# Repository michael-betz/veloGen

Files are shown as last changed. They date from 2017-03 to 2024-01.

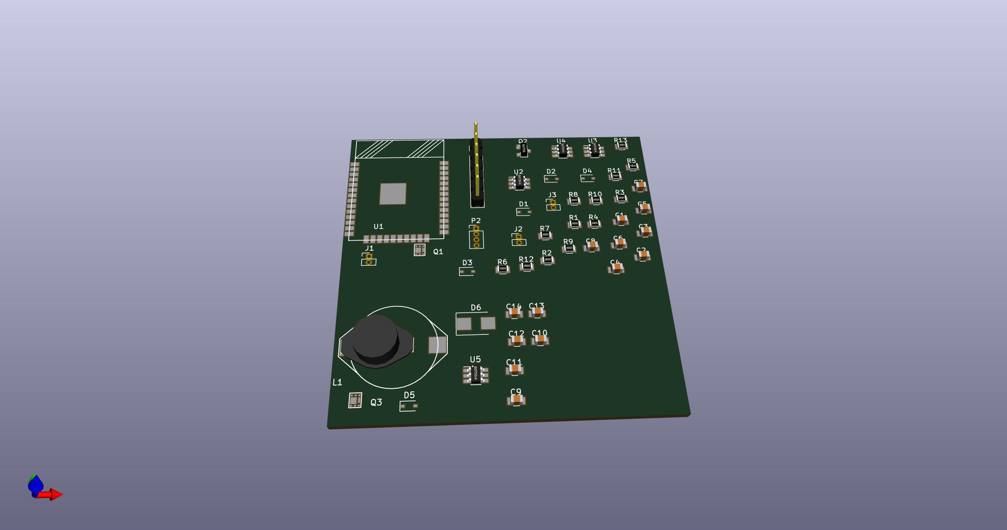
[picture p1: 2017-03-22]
PCB/3D_progress/01.jpg

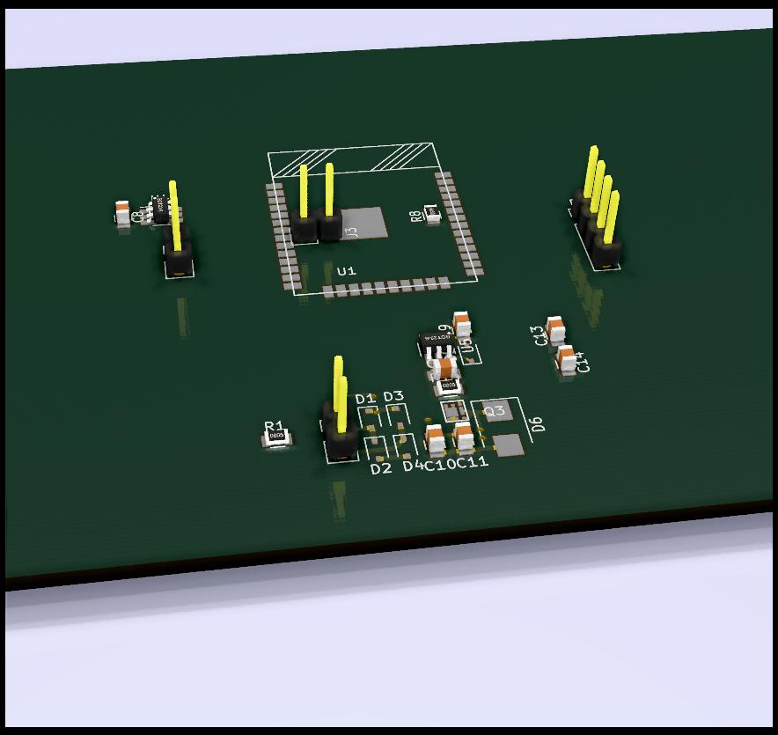
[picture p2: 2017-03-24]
PCB/3D_progress/03.jpg

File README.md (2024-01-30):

# veloGen
Minimalist bike computer and hub dynamo power manager.

A typical hub dynamo can deliver approx. 6 - 10 V at 0.5 A. Output current is inductively limited and stays relatively stable over speed. However voltage will go up. A custom made buck converter is used to extract maximum power and charge a 18650 liion cell. The front and back bike lights will be powered by this cell.

Speed and distance is tracked by measuring the zero crossings of the hub dynamo AC output. Data is collected in the CPU until read out by a mobile device over bluetooth and possibly published to a cloud service.

# Brainstorming

 * Will use ESP-WROOM-32 and make good use of the sleep modes
 * AC input zero crossing --> falling edge interrupt. Wake up CPU and increment counting reg.
 * Every second, keep track of:
   * Battery voltage. --> ADC + voltage divider to 3 V
   * Generator RMS(or peak) voltage. --> ADC + voltage divider to 3 V
   * Generator RMS current. --> 5 mOhm shunt + TS1101 + ADC 1 V
   * Battery current in and out --> 5 mOhm shunt + TS1101 + ADC 1 V
   * Realtime clock timestamp
* Store these datasets in a circular buffer in memory, until read out over BLE.
* Manage the Buck converter PWM to charge the battery with maximum current

## PCB

 * 3.3 V LDO
 * WROOM-32
 * Buck inductor
 * Buck Schottky: STPS3L40UF
 * High side mosfet driver: LTC4440-5 in SOT-23
 * High side Mosfet: STL6N3LLH6
 * 4 x schottky diode for bridge rectifier
 * Smoothing cap (10 uF?)
 * 2 x current sensing shunt (Igenerator, Ibattery) + 2 x TS1101
 * IN system programming pins
 * P - channel mosfet to switch off external power on fault (low battery / overcurrent)

### Datasheets
 * [MCP1630](http://ww1.microchip.com/downloads/en/DeviceDoc/21896b.pdf)
 * [LiIon app note](http://ww1.microchip.com/downloads/en/DeviceDoc/51555b.pdf)

## 3D printed case

 * Mounts with zip ties / verlcro straps on the frame between 2 tubes angeled at 120 deg
 * 2 Shellswhich clip / screw together
 * 5 mm wall thickness with a groove to place an O-ring between the shells
 * AC input cable (2 pin)
 * DC output + I2C cable (4 pin)

# Rev1 Notes
  * Need mounting holes on PCB
  * Case clamping the PCB doesn't work like that
  * Case make teeth tighter
  * Need to find less huge connectors for battery, dynamo and I2C
  * Add OLED to case (Case and PCB can be made wider)

# Bringup (rev1)
  * connect pogo pin adapter to board and USB serial cable
  * force flash voltage to 3.3V

```bash
$ espefuse.py set_flash_voltage 3.3V
espefuse.py v2.7
Connecting........_____....._
Enable internal flash voltage regulator (VDD_SDIO) to 3.3V.
The following efuses are burned: XPD_SDIO_FORCE, XPD_SDIO_REG, XPD_SDIO_TIEH.
This is an irreversible operation.
Type 'BURN' (all capitals) to continue.
BURN
VDD_SDIO setting complete.

$ esptool.py flash_id
esptool.py v2.7
Found 1 serial ports
Serial port /dev/ttyUSB0
Connecting........__
Detecting chip type... ESP32
Chip is ESP32D0WDQ5 (revision 1)
Features: WiFi, BT, Dual Core, 240MHz, VRef calibration in efuse, Coding Scheme None
Crystal is 40MHz
MAC: 40:f5:20:5c:8d:48
Uploading stub...
Running stub...
Stub running...
Manufacturer: c8
Device: 4018
Detected flash size: 16MB
Hard resetting via RTS pin..
```

  * `pio run -t uploadfs`
  * `pio run -t upload -t monitor`

You should see velogen booting up in the terminal.

# Changes to add for REV2

  * add 200k pulldown and 10 nF RC filter to speed sense pin
  * add Zener diode across supply rail
  * real buttons
  * better connectors (waterproofing)
  * Switchable battery power output for front light?
  * Switchable 5 V output for WS2812

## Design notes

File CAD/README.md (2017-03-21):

# Some notes about the case
  * Some kind of strapping system to attach to bike frame
  * Make the case slightly parametric to adapt to angles / dimensions of different bike frames
  * Case needs to be at least splash - waterproof
    * That means some kind of gasket / o-ring between the half shells
  * Waterproof PCB connectors? Never saw such a thing
    * AC input
    * DC out (to front light)
    * DC out (to back light)
    * Maybe just one DC out and split externally
  * Model the whole thing in Fusion360? Is there an open source alternative?

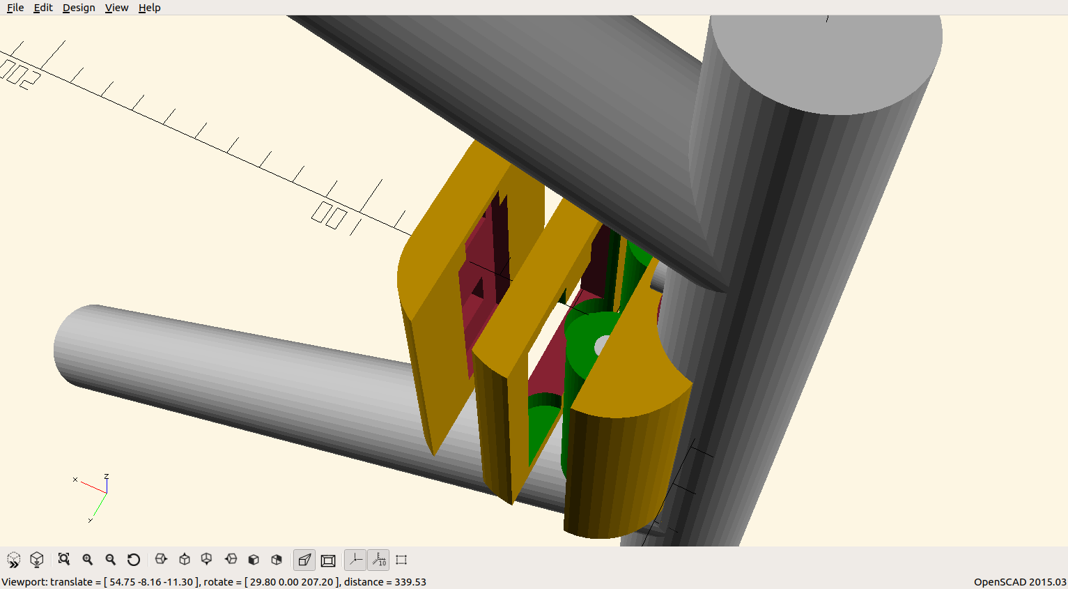
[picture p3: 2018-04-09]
CAD/scr.png

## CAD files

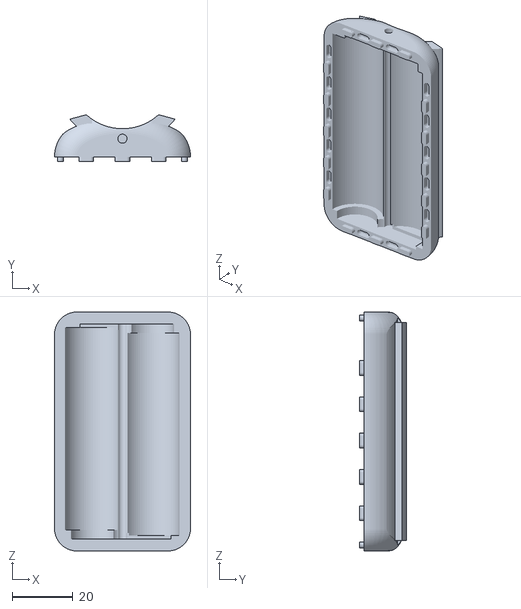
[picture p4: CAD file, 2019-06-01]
CAD/lipoShell4_lower.stl
45.0 x 15.4 x 79.0

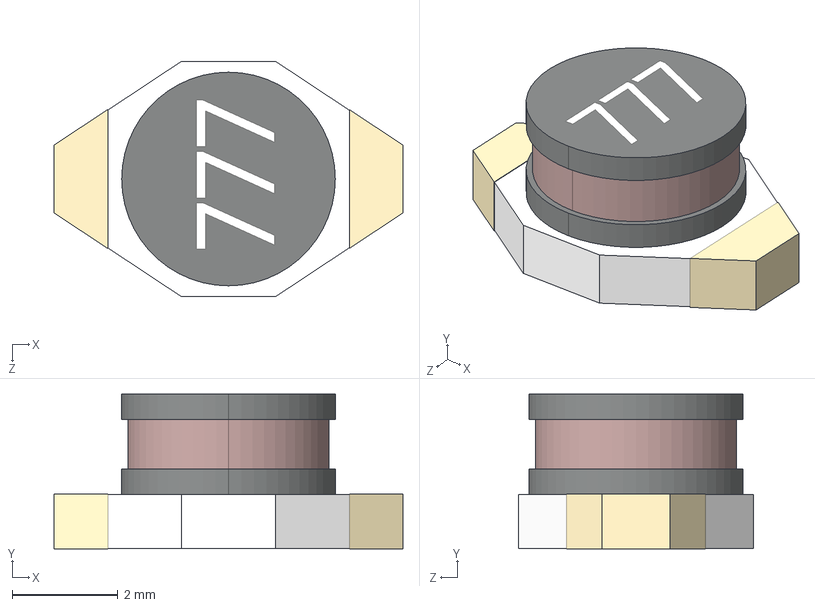
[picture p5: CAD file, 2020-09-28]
PCB2/Coilcraft-DO1608C.step
6.60 x 2.93 x 4.45 mm

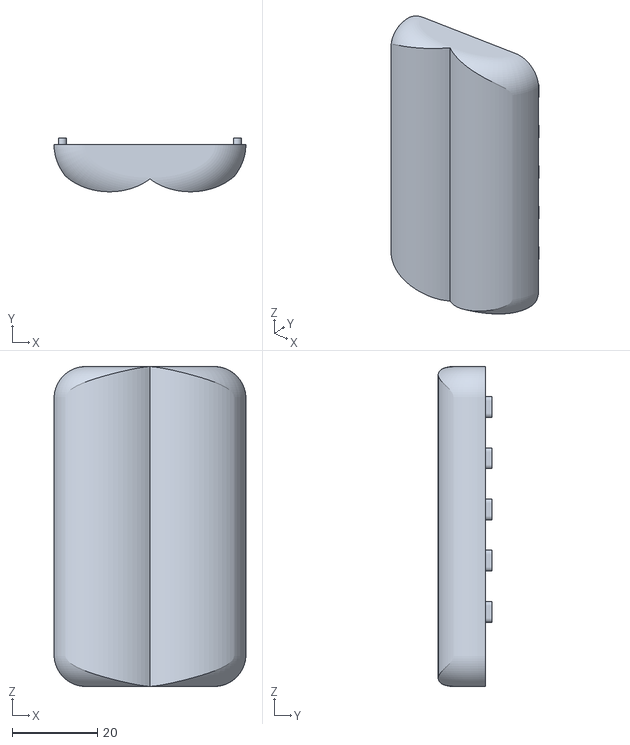
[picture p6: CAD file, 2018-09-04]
CAD/lipoShell3_upper.stl
45.0 x 12.6 x 75.0

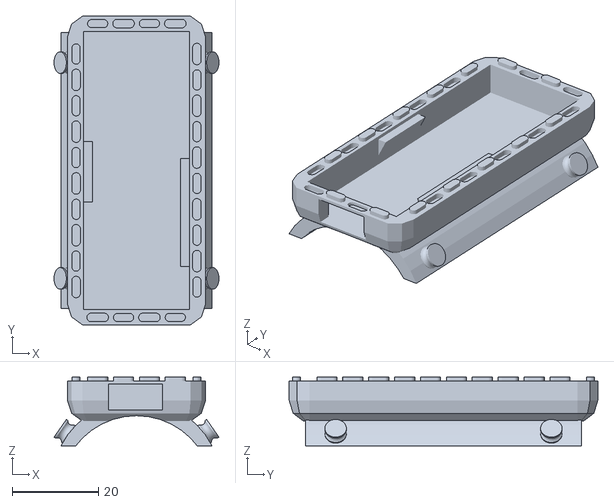
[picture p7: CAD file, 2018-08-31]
CAD/pcbShell_lower.stl
38.2 x 71.5 x 15.9

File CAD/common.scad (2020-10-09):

$fn=75;

// Bike frame mock-up
rPipe = 35.4 / 2;  // vertical pipe
// rPipe = 32.1 / 2; // horizontal pipe

module bikeFrame() {
  color("DarkGray") union() {
    // Frame
    cylinder(h=250, r=rPipe, center=true);
    translate([0,0,-(50+rPipe)]) rotate([0,120,0]) cylinder(h=300, r=rPipe);
    translate([0,0, (50+rPipe)]) rotate([0, 70,0]) cylinder(h=300, r=rPipe);
    // Nipple
    translate([0,0, 50-15]) rotate([0, 90,0]) cylinder(h=20, r=5);
  }
}

// To generate the interlocking teeth between half shells
module teeth(scaleF=1.0, n=20, raster=12) {
  for (i = [0:n-1]){
    xTooth = (i - (n - 1) / 2) * raster;
    translate([xTooth,0,0]) scale(scaleF) union(){
        translate([1.5, 0, 0]) cylinder(h=3, r=1, center=true);
        cube(size=[3, 2, 3], center=true);
        translate([-1.5, 0, 0]) cylinder(h=3, r=1, center=true);
    }
  }
}

module pin(){
    difference(){
        cylinder(r=2.5, h=4.5);
        // Donut
        translate([0, 0, 3.2]) rotate_extrude() translate([3, 0, 0]) circle(r=1);
        // translate([-5, 0, 6]) rotate([0, 45, 0]) cube(size=[10, 10, 10], center=true);
    }
}

// D shaped, shall conform to bike frame
module holder(r_outer){
    difference(){
        union(){
            translate([0, 0, -9]) rotate([90, 0, 0]) cylinder(r=r_outer+2, h=64, center=true);
            // translate([-15.0,  25, 0]) rotate([0, -65, 0]) pin();
            // translate([-15.0, -25, 0]) rotate([0, -65, 0]) pin();
            // translate([ 15.0,  25, 0]) rotate([0,  65, 0]) pin();
            // translate([ 15.0, -25, 0]) rotate([0,  65, 0]) pin();
        }
        translate([0, 0, -25]) cube(size=[50, 100, 50], center=true);
    }
}

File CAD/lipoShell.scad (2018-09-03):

include<common.scad>

// Lipo battery mockup
module lipo() {
  union() {
    color("green") cylinder(h=65.75, r=18.5/2, center=true);
    color("silver") translate([0,0,65.75/2]) cylinder(h=1, r=4, center=true);
  }
}


module lipoInnerSpace(){
  scale(1.02) translate([0, 0, 33]) lipo();
  scale(1.02) translate([0, 0, -33]) lipo();
}


module lipoHalfShell(cylOffset=0, isMirror=false){
  difference(){
    // Outer shell
    minkowski(){
      translate([0, cylOffset, 0]) cylinder(h=125, r=5, center=true);
      sphere(10);
    }
    // Cut in half
    translate([0, -15, 0]) cube(size=[30, 30, 200], center=true);
    // Inner spaces
    if(isMirror){
      mirror([0, 0, 1]) lipoInnerSpace();
    } else {
      lipoInnerSpace();
    }
    // Teeth holes
    translate([-12.5, 0, -3]) rotate([90, 90, 0]) scale([1, 1, 1.2]) teeth(n=11);
    translate([ 12.5, 0,  3]) rotate([90, 90, 0]) scale([1, 1, 1.2]) teeth(n=11);
  }
  // Teeth
  translate([-12.5, 0,  3]) rotate([90, 90, 0]) teeth(0.94, n=11);
  translate([ 12.5, 0, -3]) rotate([90, 90, 0]) teeth(0.94, n=11);
}

module lipoShell(){
  difference(){
    lipoHalfShell(4);
    // Bike frame cutout
    translate([0, 28, 0]) cylinder(h=200, r=rPipe, center=true);
  }
  %translate([0, 0, 0]) rotate([180, 0, 0]) lipoHalfShell(-4, isMirror=true);
  // Lipo Mockup
  // translate([0, 0, -33.1]) lipo();
  // translate([0, 0,  33.1]) lipo();
}

lipoShell();

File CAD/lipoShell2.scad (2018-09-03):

include<common.scad>
cylOffset=7;

// Lipo battery mockup
module lipo() {
  union() {
    color("green") cylinder(h=65.75, r=18.5/2, center=true);
    color("silver") translate([0,0,65.75/2]) cylinder(h=1, r=4, center=true);
  }
}

module outerSkin(){
  minkowski(){
      translate([0, cylOffset, 0]) cylinder(h=60, r=8, center=true);
      sphere(15);
  }
}

module lipoHalfShell(isMirror=false){
  difference(){
    // Outer shell
    outerSkin();
    // Cut in half
    // translate([0, -50, 0]) cube(size=[100, 100, 100], center=true);
    // Inner spaces
    scale(0.95) hull() case2();
    translate([-10, 0, 0]) lipo();
    translate([ 10, 0, 0]) lipo();
  }
}

module lipoShell(){
  difference(){
    lipoHalfShell(-7);
    // Bike frame cutout
    translate([0, 26, 0]) cylinder(h=200, r=rPipe, center=true);
  }
  // %translate([0, 0, 0]) rotate([180, 0, 0]) lipoHalfShell(-4, isMirror=true);
  // Lipo Mockup
  // translate([0, 0, -33.1]) lipo();
  // translate([0, 0,  33.1]) lipo();
}

module case1(){
  difference(){
    translate([11.1, 18, 53]) rotate([0, 90, 180]) import("./battery holder/files/18650_V2.STL");
    translate([0, 0, 53]) cube(size=[30, 40, 20], center=true);
  }
}

module case2(){
  intersection(){
    difference(){
      union() {
        translate([-10.5, 0, 0]) case1();
        translate([ 10.5, 0, 0]) case1();
      }
      translate([0, -15, 10]) cube(size=[0.5, 20, 50], center=false);
    }
    scale(0.95) outerSkin();
  }
}



intersection(){
  union(){
    case2();
    // lipoHalfShell();
  }
  // translate([0, 100, 30]) cube(size=[200, 200, 50], center=true);
}

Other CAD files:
CAD/lipoShell3.scad
CAD/lipoShell4.scad
CAD/main.scad
CAD/pcbShell.scad
CAD/test.scad

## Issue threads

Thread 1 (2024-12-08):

current state of the project and feature ideas

cl0rm, 2024-12-08:
Hi,

how is the current state of this project? Does it run somewhat well / stable?
I'm developing hardware as well as software/firmware so I should be able to contribute here.

I've always wanted to build something very similar to this myself.

Two extra features that might be useful would be
- google "find my" integration as soon as more information is available about it (specs are open AFAIK- contrary to apple's implementation)
- maybe GPS tracking. I've build custom GPS devices using ublox modules in the past, the hardware implementation is rather straight forward and the energy usage moderate, but it requires rather large antennas to be useful

michael-betz, 2025-01-07:
Hi!

> how is the current state of this project? Does it run somewhat well / stable?

I have it on one of my bikes and it runs stable there.

I'm happy with the animated rear-light feature, changing color / animation as a function of speed.

Online telemetry over MQTT works well as long as the ESP is connected to a hotspot.
I never got the offline caching to work reliably (the flash would corrupt after a few weeks) and turned it off.

There are still many things on the TODO list ...

I wanted to see if I can send a few kB of data back on public WIFI hot-spots using DNS tunneling.

If that works, the idea was to implement tracking based on a log of received SSIDs. But this would require to solve the corrupted flash issue first.

Another thing that I haven't quite figured out yet is how to fully waterproof the electronics and especially the connectors while keeping everything compact.

Anyway, happy to see you are interested and I love your ideas! Feel free to use my code as a starting point.

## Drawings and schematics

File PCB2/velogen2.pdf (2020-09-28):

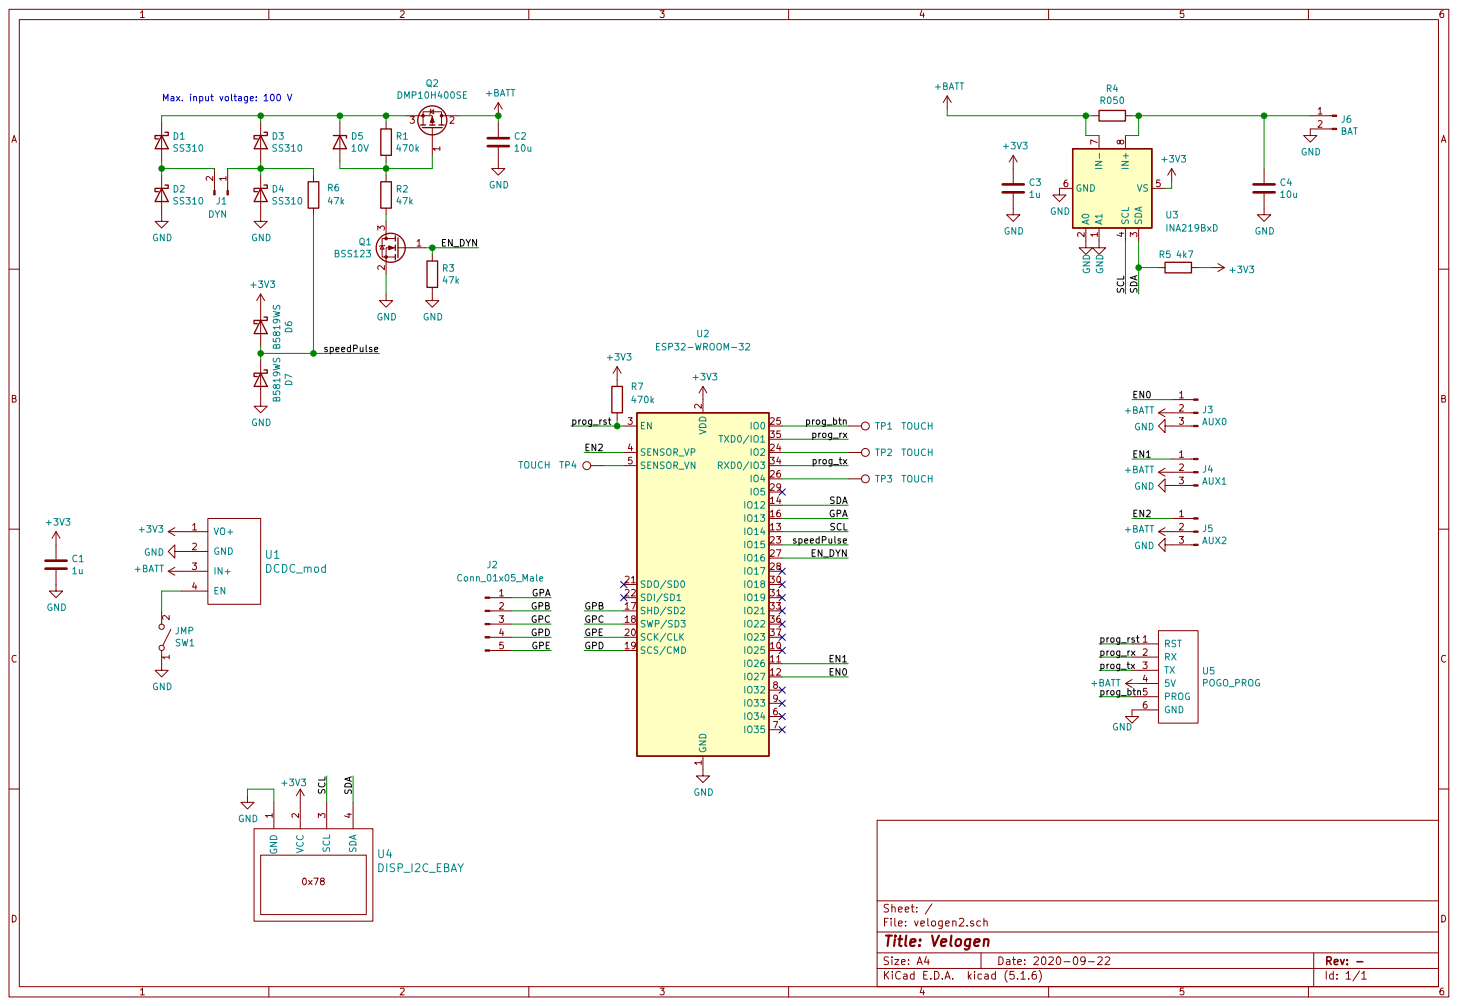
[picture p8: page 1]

4 VS 5 GND 6 IN- 7 IN+

2 SCK/CLK 20 SDO/SD0 21 SDI/SD1 22

JMP GND
File: velogen2.sch Sheet: / +BATT

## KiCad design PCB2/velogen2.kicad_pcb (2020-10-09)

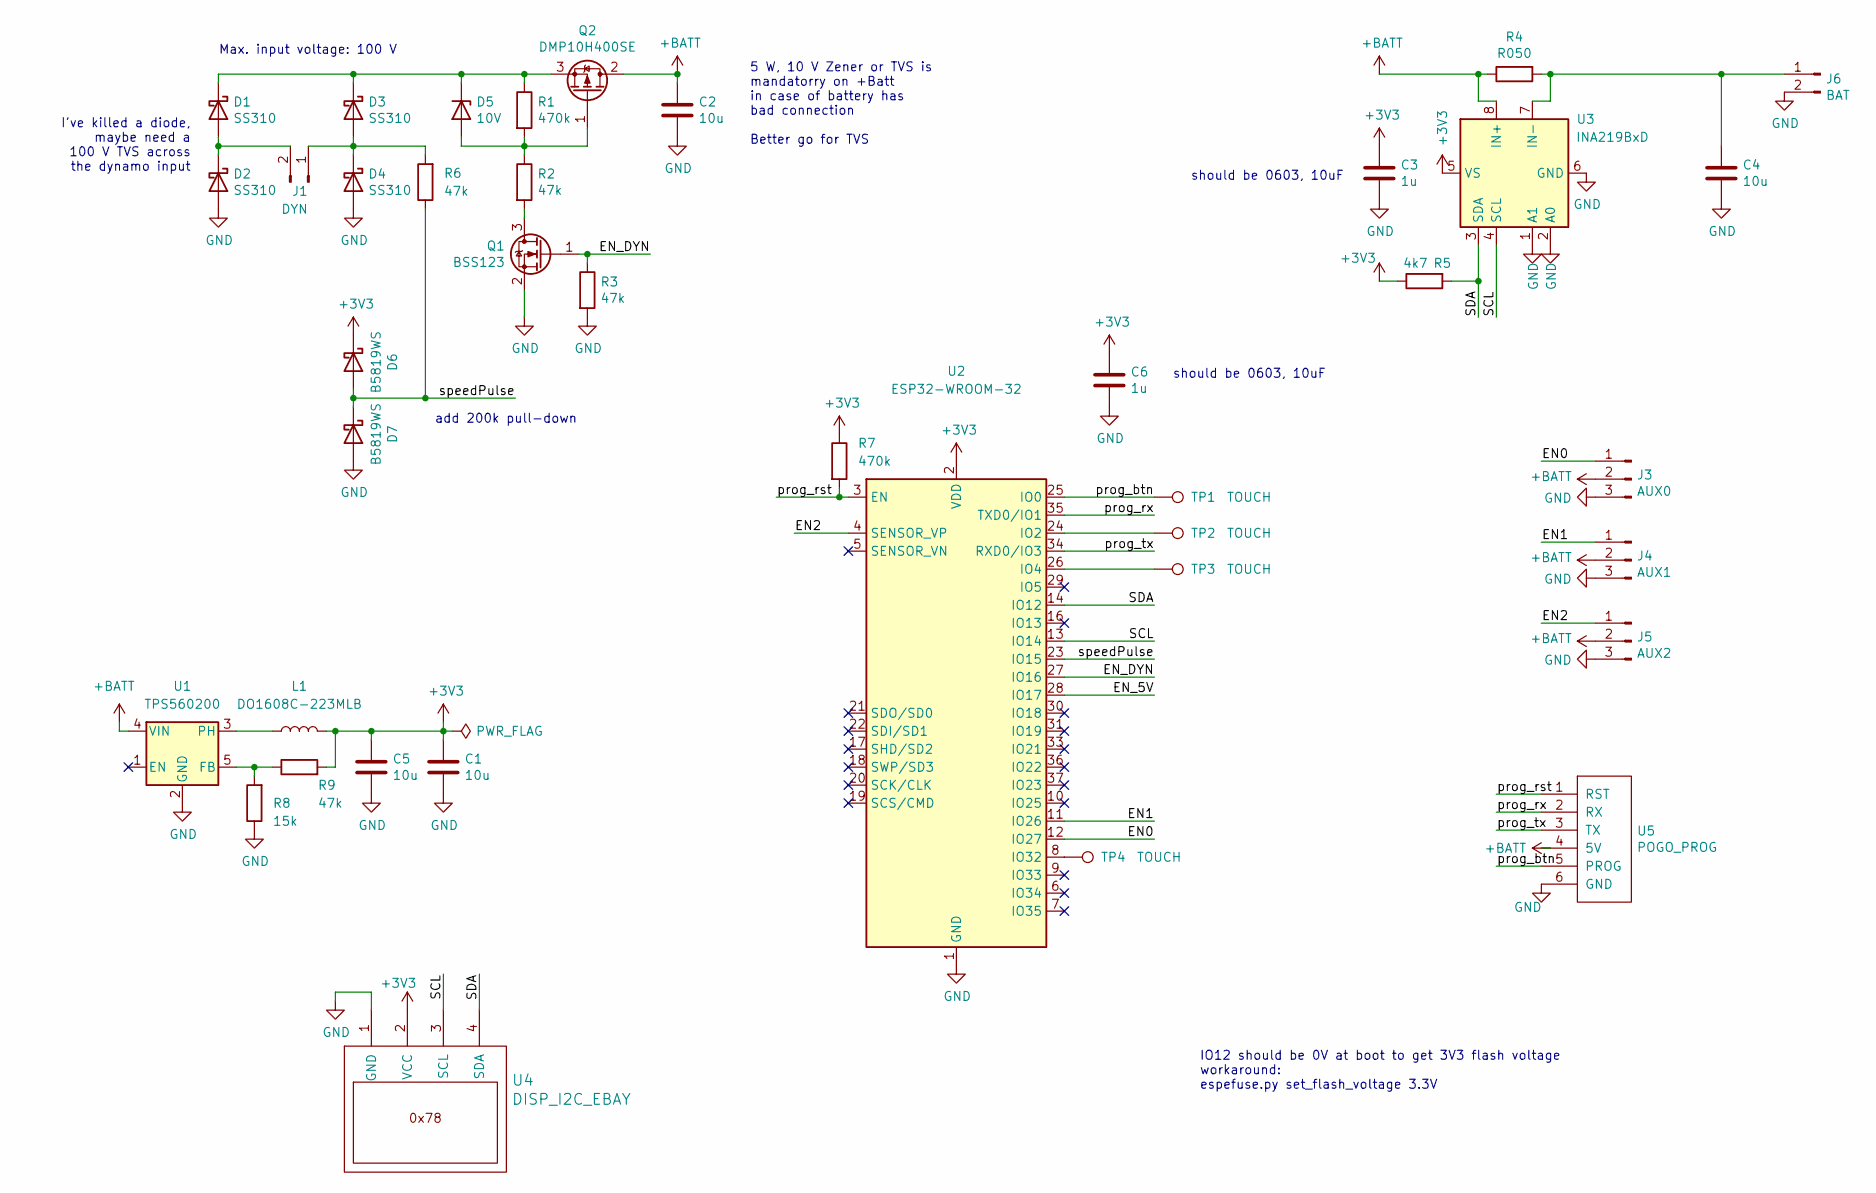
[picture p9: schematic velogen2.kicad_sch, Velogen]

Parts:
C1, C5: 10u; C_0603_1608Metric
C2, C4: 10u; C_1210_3225Metric
C3, C6: 1u; C_0805_2012Metric
D1, D2, D3, D4: SS310; D_SMA
D5: 10V; D_SOD-123
D6, D7: B5819WS; D_SOD-323
J1: DYN; JST_XH_S2B-XH-A-1_1x02_P2.50mm_Horizontal
J3: AUX0; JST_XH_S3B-XH-A-1_1x03_P2.50mm_Horizontal
J4: AUX1; JST_XH_S3B-XH-A-1_1x03_P2.50mm_Horizontal
J5: AUX2; JST_XH_S3B-XH-A-1_1x03_P2.50mm_Horizontal
J6: BAT; JST_XH_S2B-XH-A-1_1x02_P2.50mm_Horizontal
L1: DO1608C-223MLB; DO1608
Q1: BSS123; SOT-23
Q2: DMP10H400SE; SOT-223-3_TabPin2
R1, R7: 470k; R_0805_2012Metric
R2, R3, R6, R9: 47k; R_0805_2012Metric
R4: R050; R_1206_3216Metric
R5: 4k7; R_0805_2012Metric
R8: 15k; R_0805_2012Metric
TP1, TP2, TP3, TP4: TOUCH; TestPoint_THTPad_D1.5mm_Drill0.7mm
U1: TPS560200; SOT-23-5
U2: ESP32-WROOM-32
U3: INA219BxD; SOIC-8_3.9x4.9mm_P1.27mm
U4: DISP_I2C_EBAY
U5: POGO_PROG; myPogoPads

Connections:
+3V3: C1.1, C3.1, C5.1, C6.1, D6.1 (K), L1.2, R5.1, R7.1, R9.2, U2.2 (VDD), U3.5 (VS), U4.2 (VCC)
+BATT: C2.1, J3.2, J4.2, J5.2, Q2.2 (D), R4.1, U1.4 (VIN), U3.8 (IN+), U5.4 (5V)
/EN0: J3.1, U2.12 (IO27)
/EN1: J4.1, U2.11 (IO26)
/EN2: J5.1, U2.4 (SENSOR_VP)
/EN_DYN: Q1.1 (G), R3.1, U2.27 (IO16)
/SCL: U2.13 (IO14), U3.4 (SCL), U4.3 (SCL)
/SDA: R5.2, U2.14 (IO12), U3.3 (SDA), U4.4 (SDA)
/prog_btn: TP1.1, U2.25 (IO0), U5.5 (PROG)
/prog_rst: R7.2, U2.3 (EN), U5.1 (RST)
/prog_rx: U2.35 (TXD0/IO1), U5.2 (RX)
/prog_tx: U2.34 (RXD0/IO3), U5.3 (TX)
/speedPulse: D6.2 (A), D7.1 (K), R6.1, U2.23 (IO15)
GND: C1.2, C2.2, C3.2, C4.2, C5.2, C6.2, D2.2 (A), D4.2 (A), D7.2 (A), J3.3, J4.3, J5.3, J6.2, Q1.2 (S), R3.2, R8.1, U1.2 (GND), U2.1 (GND), U2.15 (GND), U2.38 (GND), U2.39 (GND), U3.1 (A1), U3.2 (A0), U3.6 (GND), U4.1 (GND), U5.6 (GND)
unnamed: C4.1, J6.1, R4.2, U3.7 (IN-)
unnamed: D1.1 (K), D3.1 (K), D5.1 (K), Q2.3 (S), R1.1
unnamed: D1.2 (A), D2.1 (K), J1.2
unnamed: D3.2 (A), D4.1 (K), J1.1, R6.2
unnamed: D5.2 (A), Q2.1 (G), R1.2, R2.1
unnamed: L1.1, U1.3 (PH)
unnamed: Q1.3 (D), R2.2
unnamed: R8.2, R9.1, U1.5 (FB)
unnamed: TP2.1, U2.24 (IO2)
unnamed: TP3.1, U2.26 (IO4)
unnamed: TP4.1, U2.8 (IO32)

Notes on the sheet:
IO12 should be 0V at boot to get 3V3 flash voltage workaround: espefuse.py set_flash_voltage 3.3V
add 200k pull-down
5 W, 10 V Zener or TVS is mandatorry on +Batt in case of battery has bad connection Better go for TVS
should be 0603, 10uF
I've killed a diode, maybe need a 100 V TVS across the dynamo input
Max. input voltage: 100 V

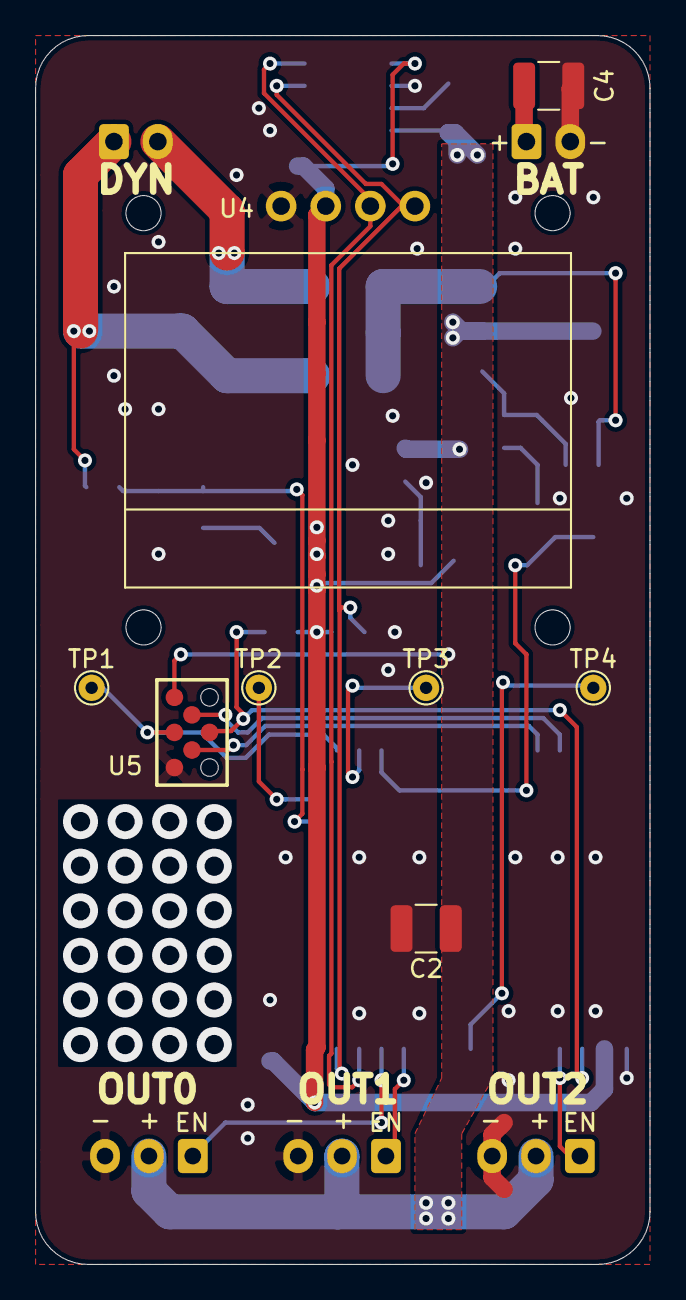
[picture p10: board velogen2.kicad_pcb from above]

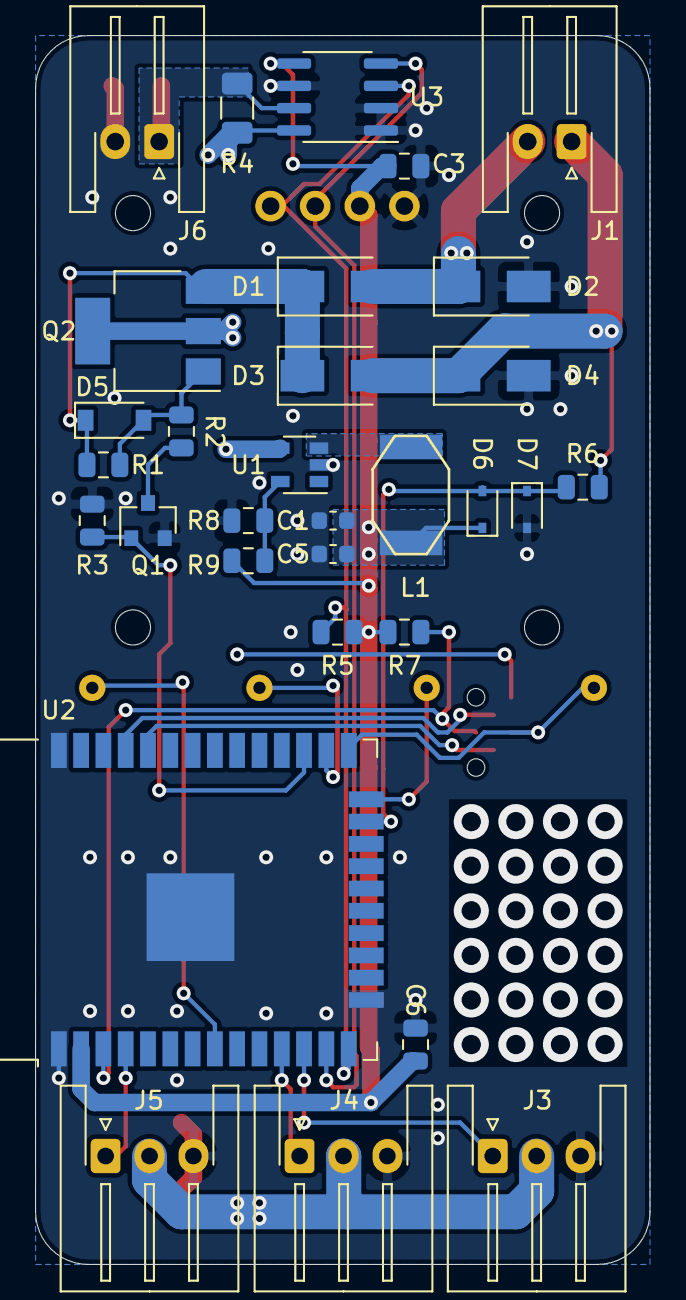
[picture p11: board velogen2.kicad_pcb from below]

Board: 2 copper layers, 35.0 x 70.0 mm, 39 parts (31 on the bottom side), 25 nets.

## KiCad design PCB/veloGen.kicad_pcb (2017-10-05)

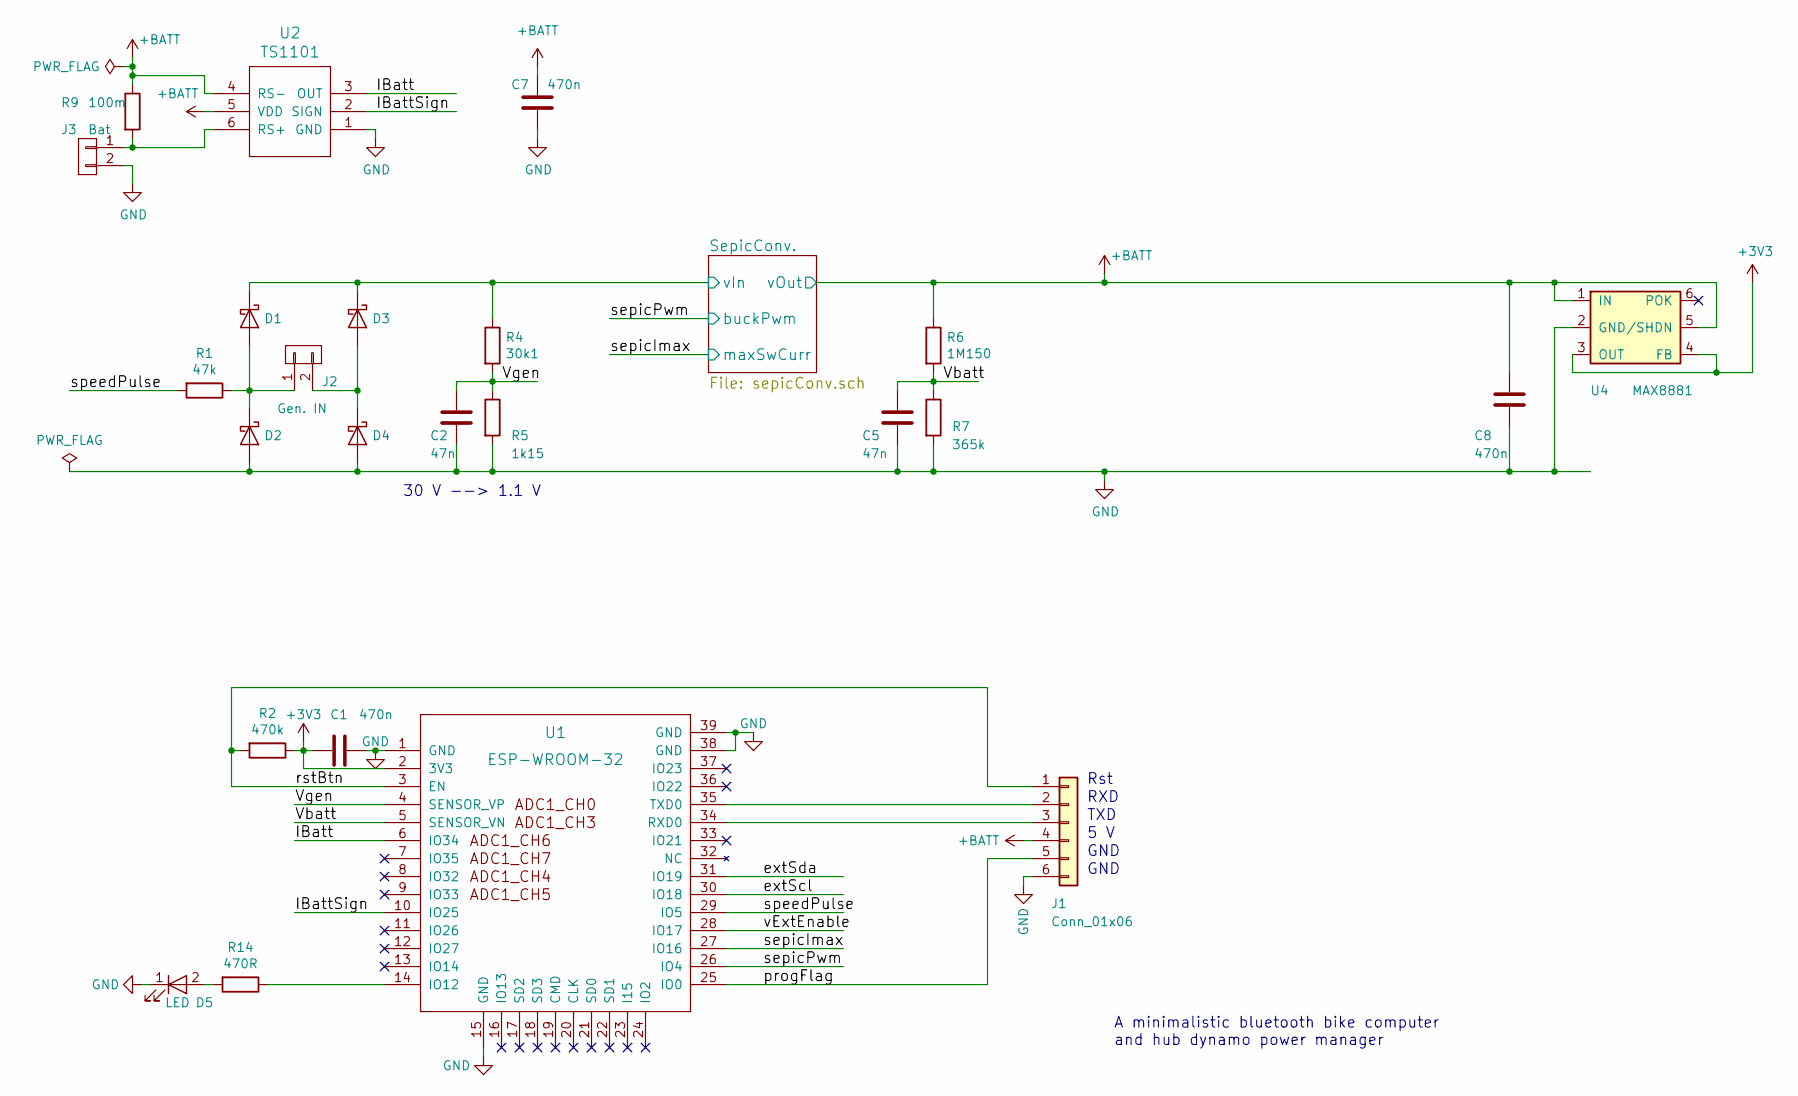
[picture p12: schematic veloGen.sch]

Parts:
C1, C7, C8: 470n; C_0805
C2, C5: 47n; C_0805
D1, D2, D3, D4: B5819WS; D_SOD-323
D5: LED; LED_0805
J1: Conn_01x06; myPogoPads
J2: Gen. IN; Pin_Header_Straight_1x02_Pitch2.54mm
J3: Bat; Pin_Header_Straight_1x02_Pitch2.54mm
R1: 47k; R_0805
R2: 470k; R_0805
R4: 30k1; R_0805
R5: 1k15; R_0805
R6: 1M150; R_0805
R7: 365k; R_0805
R9: 100m; R_1206
R14: 470R; R_0805
U1: ESP-WROOM-32
U2: TS1101; SOT-23-6_Handsoldering
U4: MAX8881; SOT-23-6

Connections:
+3V3: C1.2, R2.1, U1.2 (3V3), U4.3 (OUT), U4.4 (FB)
+BATT: C7.1, C8.1, J1.4, R6.1, R9.1, U2.4 (RS-), U2.5 (VDD), U4.1 (IN), U4.5 (/SHDN); also elsewhere on the board
/IBatt: U1.6 (IO34), U2.3 (OUT)
/IBattSign: U1.10 (IO25), U2.2 (SIGN)
/SepicConv./vIn: D1.1 (K), D3.1 (K), R4.1; also elsewhere on the board
/Vbatt: C5.1, R6.2, R7.1, U1.5 (SENSOR_VN)
/Vgen: C2.1, R4.2, R5.1, U1.4 (SENSOR_VP)
/extScl: U1.30 (IO18)
/extSda: U1.31 (IO19)
/progFlag: J1.5, U1.25 (IO0)
/rstBtn: J1.1, R2.2, U1.3 (EN)
/sepicImax: U1.27 (IO16); also elsewhere on the board
/sepicPwm: U1.26 (IO4); also elsewhere on the board
/speedPulse: R1.2, U1.29 (IO5)
/vExtEnable: U1.28 (IO17)
GND: C1.1, C2.2, C5.2, C7.2, C8.2, D2.2 (A), D4.2 (A), D5.1 (K), J1.6, J3.2, R5.2, R7.2, U1.1 (GND), U1.15 (GND), U1.38 (GND), U1.39 (GND), U2.1 (GND), U4.2 (GND); also elsewhere on the board
unnamed: D1.2 (A), D2.1 (K), J2.1, R1.1
unnamed: D3.2 (A), D4.1 (K), J2.2
unnamed: D5.2 (A), R14.2
unnamed: J1.2, U1.35 (TXD0)
unnamed: J1.3, U1.34 (RXD0)
unnamed: J3.1, R9.2, U2.6 (RS+)
unnamed: R14.1, U1.14 (IO12)

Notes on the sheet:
A minimalistic bluetooth bike computer and hub dynamo power manager
30 V --> 1.1 V
Rst
RXD
TXD
5 V
GND

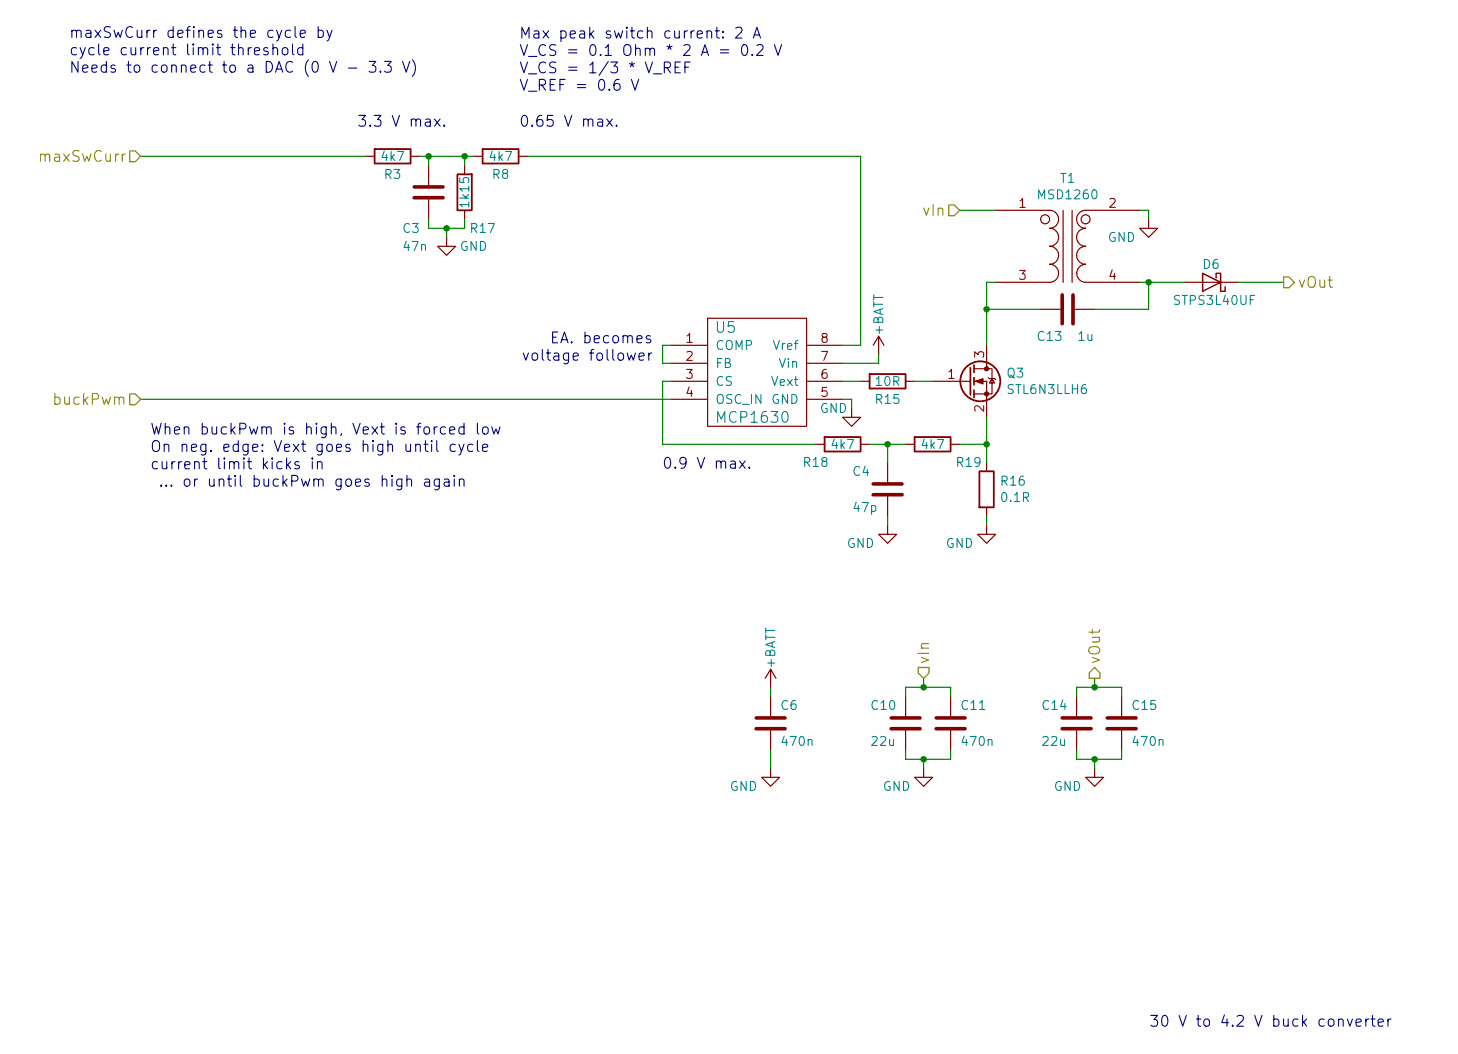
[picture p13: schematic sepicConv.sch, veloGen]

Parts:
C3: 47n; C_0805
C4: 47p; C_0805
C6, C11, C15: 470n; C_0805
C10, C14: 22u; C_1206
C13: 1u; C_0805
D6: STPS3L40UF; D_SMB_Standard
Q3: STL6N3LLH6; PowerFLAT_2x2
R3, R8, R18, R19: 4k7; R_0805
R15: 10R; R_0805
R16: 0.1R; R_1206
R17: 1k15; R_0805
T1: MSD1260
U5: MCP1630; MSOP-8_3x3mm_Pitch0.65mm

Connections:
+BATT: C6.2, C14.1, C15.2, D6.1 (K), U5.7 (Vin); also elsewhere on the board
/SepicConv./vIn: C10.1, C11.2, T1.1 (AA); also elsewhere on the board
/sepicImax: R3.2; also elsewhere on the board
/sepicPwm: U5.4 (OSC_IN); also elsewhere on the board
GND: C3.2, C4.2, C6.1, C10.2, C11.1, C14.2, C15.1, R16.2, R17.1, T1.2 (AB), U5.5 (GND); also elsewhere on the board
unnamed: C3.1, R3.1, R8.2, R17.2
unnamed: C4.1, R18.1, R19.2
unnamed: C13.1, D6.2 (A), T1.4 (SB)
unnamed: C13.2, Q3.3 (D), T1.3 (SA)
unnamed: Q3.1 (G), R15.1
unnamed: Q3.2 (S), R16.1, R19.1
unnamed: R8.1, U5.8 (Vref)
unnamed: R15.2, U5.6 (Vext)
unnamed: R18.2, U5.3 (CS)
unnamed: U5.1 (COMP), U5.2 (FB)

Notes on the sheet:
30 V to 4.2 V buck converter
When buckPwm is high, Vext is forced low On neg. edge: Vext goes high until cycle current limit kicks in ... or until buckPwm goes high again
EA. becomes voltage follower
maxSwCurr defines the cycle by cycle current limit threshold Needs to connect to a DAC (0 V - 3.3 V)
0.9 V max.
Max peak switch current: 2 A V_CS = 0.1 Ohm * 2 A = 0.2 V V_CS = 1/3 * V_REF V_REF = 0.6 V
0.65 V max.
3.3 V max.

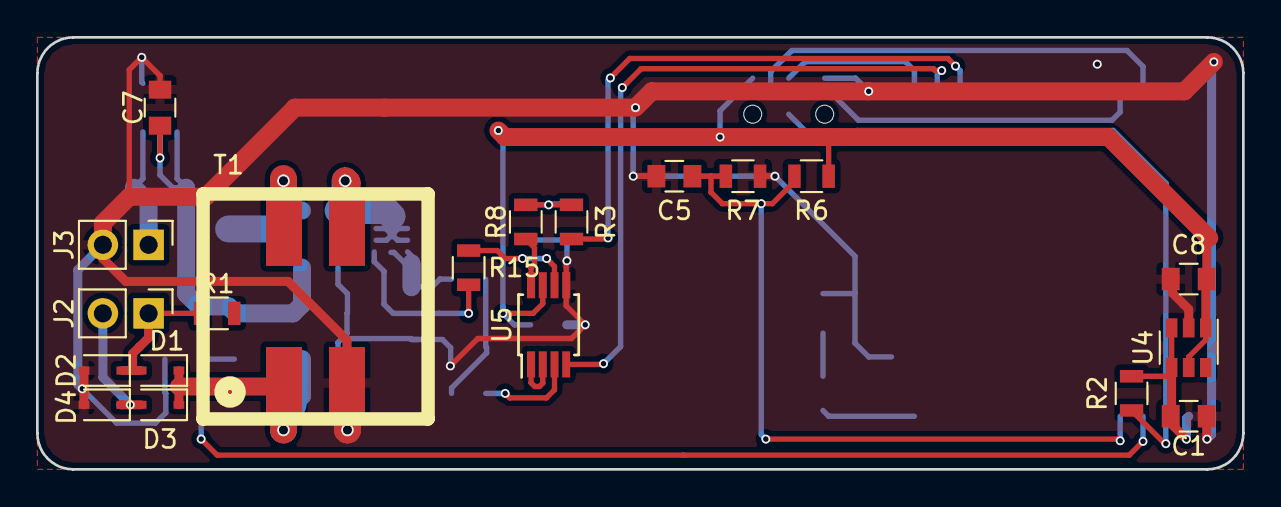
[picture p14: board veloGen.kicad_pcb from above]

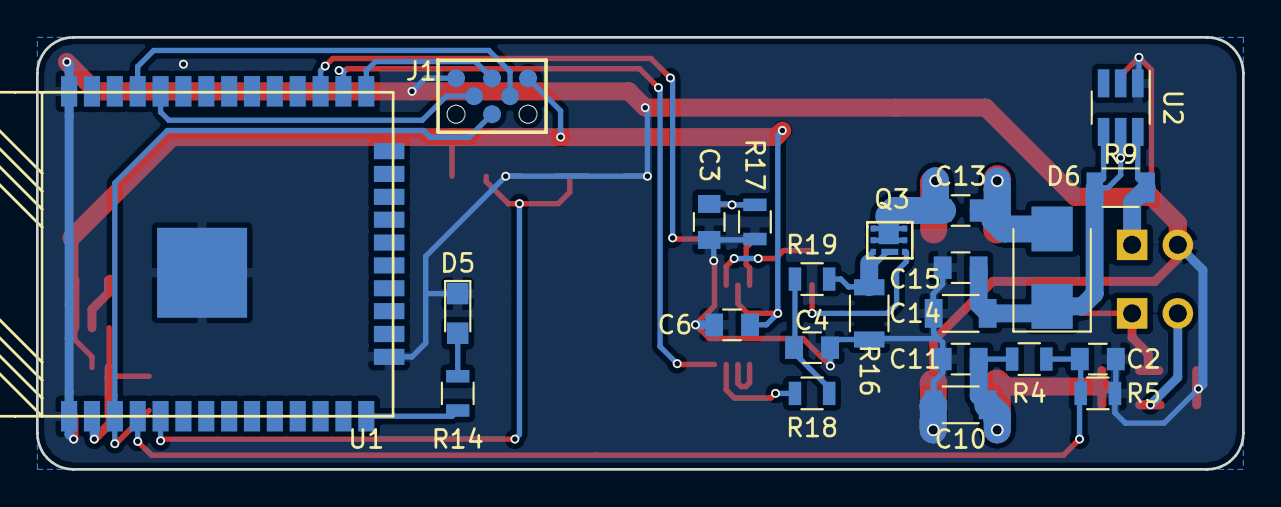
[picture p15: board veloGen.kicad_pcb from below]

Board: 2 copper layers, 67.0 x 24.0 mm, 43 parts (23 on the bottom side), 30 nets.

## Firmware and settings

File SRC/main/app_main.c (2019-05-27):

// Copyright 2017 Espressif Systems (Shanghai) PTE LTD
//
// Licensed under the Apache License, Version 2.0 (the "License");
// you may not use this file except in compliance with the License.
// You may obtain a copy of the License at
//
//     http://www.apache.org/licenses/LICENSE-2.0
//
// Unless required by applicable law or agreed to in writing, software
// distributed under the License is distributed on an "AS IS" BASIS,
// WITHOUT WARRANTIES OR CONDITIONS OF ANY KIND, either express or implied.
// See the License for the specific language governing permissions and
// limitations under the License.

#include <string.h>
#include <stdio.h>
#include <stdlib.h>
#include <math.h>
#include <time.h>
#include "driver/gpio.h"
#include "driver/ledc.h"
#include "driver/sigmadelta.h"
#include "libesphttpd/esp.h"
#include "libesphttpd/cgiwebsocket.h"
#include "esp_log.h"
#include "esp_sleep.h"
#include "web_console.h"
#include "wifi_startup.h"
#include "velogen_hw.h"
#include "app_main.h"

static const char *T = "MAIN_APP";

static void wsAppReceive(Websock *ws, char *data, int len, int flags){
    int temp;
    if(len>1){
        switch(data[0]){
            case 'p':
                temp = atoi(&data[1]);
                set_duty(temp);
                break;
            case 'I':
                temp = atoi(&data[1]);
                set_dac(temp);
                break;
            case 'w':
                if (data[1] == 'h') {
                    ESP_LOGI(T, "Switching to hot-spot mode");
                    wifiState = WIFI_START_HOTSPOT_MODE;
                } else if (data[1] == 'a') {
                    ESP_LOGI(T, "Switching to station mode");
                    wifiState = WIFI_CON_TO_AP_MODE;
                }
            default:
                ESP_LOGI(T, "wsrx:");
                ESP_LOG_BUFFER_HEXDUMP(T, data, len, ESP_LOG_INFO);
        }
    }
}

// Websocket connected.
void wsAppConnect(Websock *ws) {
    uint8_t *rip = ws->conn->remote_ip;
    ESP_LOGI(T,"WS-APP-client: %d.%d.%d.%d", rip[0], rip[1], rip[2], rip[3] );
    ws->recvCb = wsAppReceive;
}

void app_main(){
    gpio_set_level( GPIO_LED, 1 );

    //------------------------------
    // Enable RAM log file
    //------------------------------
    esp_log_level_set("*", ESP_LOG_DEBUG);
    esp_log_set_vprintf(wsDebugPrintf);

    //------------------------------
    // Init filesystems
    //------------------------------
    initSpiffs();

    //------------------------------
    // Velogen stuff
    //------------------------------
    if(esp_sleep_get_wakeup_cause() == ESP_SLEEP_WAKEUP_UNDEFINED){
        ESP_LOGI(T, "************* Woke up from the DEEEEAAADD *************");
    } else {
        ESP_LOGI(T, "ZZzzZZZZzzzZZZZzZzz Woke up from a deep nap ZZzzzzZZZzzzzZZZz");
    }
    initVelogen();

    //------------------------------
    // Startup wifi & webserver
    //------------------------------
    ESP_LOGI(T,"Starting network infrastructure ...");
    wifi_conn_init();
    xEventGroupWaitBits(wifi_event_group, CONNECTED_BIT, 0, 0, 20000/portTICK_PERIOD_MS);
    // vTaskDelay(3000 / portTICK_PERIOD_MS);

    //------------------------------
    // Set the clock / print time
    //------------------------------
    // Set timezone to Eastern Standard Time
    setenv("TZ", "PST8PDT", 1);
    tzset();

    xTaskCreate(&adc_monitor_task, "adc_monitor_task", 2048, NULL, 5, NULL);
    ESP_LOGI(T, "Done");
    gpio_set_level(GPIO_LED, 0);
}

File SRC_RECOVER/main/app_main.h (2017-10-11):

#ifndef APP_MAIN_H
#define APP_MAIN_H

#define GPIO_IBATT_SIGN 25
#define GPIO_EXT_SDA	27
#define GPIO_EXT_SCL	14
#define GPIO_LED		12
#define GPIO_SEPIC_PWM	 4
#define GPIO_SEPIC_IMAX	16
#define GPIO_SPEED_PLS	 5
#define ADC_CH_VGEN	 	 0
#define ADC_CH_VBATT 	 3
#define ADC_CH_IBATT 	 6

#define STARTUP_DAC_VALUE  -80
#define STARTUP_DUTY_VALUE  50

#endif

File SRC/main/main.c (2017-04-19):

#include "freertos/FreeRTOS.h"
#include "freertos/event_groups.h"
#include "esp_system.h"
#include "nvs_flash.h"
#include "driver/gpio.h"
#include "driver/adc.h"
#include "esp_log.h"
#include <string.h>

#include "lwip/err.h"
#include "lwip/sockets.h"
#include "lwip/sys.h"
#include "lwip/netdb.h"
#include "lwip/dns.h"

#include "main.h"
#include "debugUdp.h"
#include "buckPwm.h"

static const char* TAG = "main.c";

/* Variable holding number of times ESP32 restarted since first boot.
 * It is placed into RTC memory using RTC_DATA_ATTR and
 * maintains its value when ESP32 wakes from deep sleep.
 */
RTC_DATA_ATTR uint32_t boot_count = 0;
//
static void adc_monitor_task(void *pvParameters)
{
    adc1_config_width( ADC_WIDTH_12Bit );
    adc1_config_channel_atten( ADC_VBATT_CHANNEL, ADC_ATTEN_0db );

    uint32_t adcVal, i;
    while (true) {
        adcVal = 0;
        for ( i=0; i<32; i++ ){
        	adcVal += adc1_get_voltage(ADC_VBATT_CHANNEL);
        }
        adcVal /= 32;
        ESP_LOGI( TAG, "%4d  v_batt = %d mV (%d)", boot_count++, ADC_GET_VBATT(adcVal), adcVal );

        vTaskDelay( 2500 );
    }
}
//
//static void gen_monitor_task(void *pvParameters)
//{
//	uint8_t val=0, temp=0;
//	ESP_ERROR_CHECK( gpio_set_direction(GEN_GPIO, GPIO_MODE_INPUT) );
//	ESP_ERROR_CHECK( gpio_set_pull_mode(GEN_GPIO, GPIO_FLOATING)   );
//
//    while (true) {
//    	temp = gpio_get_level(GEN_GPIO);
//    	if(  temp != val ){
//    		val = temp;
//    		gpio_set_level( LED_GPIO, temp );
//	        ESP_LOGI( TAG, "%d", temp );
//    	}
//        vTaskDelay( 2 );
//    }
//}
//

static void pwmFun_task(void *pvParameters)
{
	initPwm();
	uint16_t pwmValue = 40;
//	setPwm( 50 );
	while(1){
		setPwm( pwmValue++ );
//		if( pwmValue > (BUCK_PWM_MAX-13) ){
		if( pwmValue > 60 ){
			pwmValue = 40;
		}
		vTaskDelay( 300 );
	}
}

void app_main(void)
{
	ESP_LOGI( TAG, "Hello World!" );
	ESP_ERROR_CHECK( nvs_flash_init() );
	// Init LED port
	gpio_pad_select_gpio( LED_GPIO );
	ESP_ERROR_CHECK( gpio_set_direction( LED_GPIO, GPIO_MODE_OUTPUT ) );
	// Init BUCK port
	gpio_pad_select_gpio( BUCK_GPIO );
	ESP_ERROR_CHECK( gpio_set_direction( BUCK_GPIO, GPIO_MODE_OUTPUT ) );

	xTaskCreate(&pwmFun_task,      "pwmFun_task",      2048, NULL, 5, NULL);

//	while(1){
//		uint8_t temp = gpio_get_level( GEN_GPIO );
//		gpio_set_level( LED_GPIO, temp );
//		vTaskDelay( 10 );
//	}
//    wifiInit();
//	xTaskCreate(&udp_debug_init,   "udp_debug_task",   2048, NULL, 5, NULL);
	xTaskCreate(&adc_monitor_task, "adc_monitor_task", 2048, NULL, 5, NULL);
//  xTaskCreate(&gen_monitor_task, "gen_monitor_task", 2048, NULL, 5, NULL);
}

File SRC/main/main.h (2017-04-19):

/*
 * main.h
 *
 *  Created on: Apr 5, 2017
 *      Author: michael
 */

#ifndef MAIN_H_
#define MAIN_H_



// Seems like we get 9 pulses per revolution
#define GEN_GPIO  GPIO_NUM_5
#define LED_GPIO  GPIO_NUM_12
#define BUCK_GPIO GPIO_NUM_4

// ADC (VBatt) calibration constants
#define ADC_VBATT_CHANNEL    3
#define ADC_M            97245
#define ADC_B         28531865
#define ADC_D           100000
#define ADC_GET_VBATT(cnt) ( ( (uint32_t)cnt * ADC_M + ADC_B ) / ADC_D ) //[mV]


#endif /* MAIN_H_ */

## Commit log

2017-03-18 Started with the Schematic
    [veloGen.kicad_pcb, veloGen.sch]
2017-03-20 Got more specific about parts
    [veloGen.sch]
2017-03-21 Started the Schematic
    [veloGen.sch]
2017-03-21 Started real schematic
2017-03-21 Refined the schematic
    [buckConv.sch]
2017-03-22 Schematic one step closer
    [buckConv.sch, veloGen.kicad_pcb, veloGen.sch]
2017-03-23 Moved around some components a bit
    [veloGen.kicad_pcb, veloGen.sch]
2017-03-24 Layout ideas
    [buckConv.sch, veloGen.kicad_pcb, veloGen.sch]
2017-03-29 Added template esp32 project
2017-04-04 80 MHz without WIFI: 26 mA
    [veloGen.sch]
2017-04-06 Played around with Hardware PWM
2017-04-07 minor stuff:
    [veloGen.sch]
2017-04-19 Added SEPIC ltspice model
    [buckConv.sch, veloGen.sch]
2017-04-20 Simulation is working (including the cycle by cycle current limit)
2017-05-25 Schematic work
    [buckConv.sch, veloGen.sch]
2017-10-04 Simplified schematic and started layout
    [buckConv.sch, sepicConv.sch, veloGen.kicad_pcb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]
2017-10-04 completed an ugly pcb with minimalistic fuctionality
    [veloGen.kicad_pcb, veloGen.sch]
2017-10-05 Added batery current sense
    [sepicConv.sch, veloGen.kicad_pcb, veloGen.sch]
2017-10-06 revised layout
    [veloGen2.kicad_pcb]
2017-10-07 moved stuff around 0.6 vias
    [sepicConv.sch, veloGen.sch, veloGen2.kicad_pcb]
2017-10-09 built first prototype, some mods are needed
    [progAdapt.kicad_pcb, progAdapt.sch, sepicConv.sch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]
2017-10-11 Fixed current measurement
2017-10-12 Cleaned up a bit
    [veloGen.sch]
2017-10-17 Fixed the linear calibration factor for VBatt
    [sepicConv.sch, veloGen.sch]
2017-10-20 Added I-sense cal constants
    [veloGen.sch]
2017-10-23 Screwed up attempt of an TFTP server. Needs to be changed to be more FreeRTOS style
    [partitions.csv]
2017-10-30 Got httpd working
    [partitions.csv]
2017-10-31 Bit of a clean up
    [partitions.csv]
2017-11-05 Quite happy with how the web console turned out
    [partitions.csv]
2017-11-06 Some bugs in directory listing
    [app_main.c]
2018-04-06 fun with openscad!
    [test.scad]
2018-04-09 open-scad is addicting!
    [test.scad]
2018-08-30 Half shell looks good
    [halfShell.scad, try2.scad]
2018-08-31 Looking good
    [common.scad, halfShell.scad, lipoShell.scad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]
2018-08-31 Printed lower shell
    [common.scad, lipoShell.scad, pcbShell.scad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]
2018-09-03 Battery case work
    [common.scad, lipoShell.scad, lipoShell2.scad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]
2018-09-04 off to the printer it goes
    [common.scad, lipoShell3.scad, lipoShell3_upper.stl]
2018-09-05 kinda works
    [partitions.csv]
2019-05-27 First bike test run. Fried the board :(
2019-06-01 new revision on battery holder
    [common.scad, lipoShell4.scad, lipoShell4_lower.stl]
2020-09-09 add second stab at velogen PCB
    [velogen2.kicad_pcb, velogen2.sch]
2020-09-09 pcbShell: adapt for larger PCB2 size
    [pcbShell.scad]
2020-09-17 Added Schottkey diode; Clean up ERC
    [velogen2.sch]
2020-09-17 PCB: Moved R2
    [velogen2.kicad_pcb]
2020-09-19 clean up schematic symbols
    * re-associate standard symbols with the standard library (needs to be
    installed)
    * remove `myStuff` library. Symbols from there are now in rescue.lib
    * make the 3V3 enable switch a jumper poking out trough the case
    [velogen2.kicad_pcb, velogen2.sch]
2020-09-19 move all small components to top side
    [velogen2.kicad_pcb]
2020-09-22 sch: fix some component names
    [velogen2.kicad_pcb, velogen2.sch]
2020-09-22 put propper package (SMA) for diodes
    [velogen2.kicad_pcb, velogen2.sch]
2020-09-23 did some routing of the power rails
    * kinda stuck on the 3V3, might need to re-consider placement
    [velogen2.kicad_pcb, velogen2.sch]
2020-09-23 top half is routed
    [velogen2.kicad_pcb]
2020-09-28 das Schwein ist bestellt!
    [Coilcraft-DO1608C.step, pcbShell.scad, velogen2.kicad_pcb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]
2020-10-09 cad: tune the PCB shell, add oled spacer
    [common.scad, pcbShell.scad, velogen2.kicad_pcb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]
2020-10-11 work on OLED gui and simulation
    [velogen2.sch]
2020-10-14 add new arduino based firmware
2020-10-15 add touch buttons to switch screens
2020-10-15 move stuff around, crude tachometer works
    ... using floats. Feels like cheating.
    [progAdapt.kicad_pcb, progAdapt.sch, sepicConv.sch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]
2020-10-18 last version using arduino
2020-10-18 clean up and move things around a bit
    [partitions.csv]
2020-10-18 add new ESP_IDF based firmware, move things around
    [partitions.csv]
2020-10-21 add OTA functionality
    * add self-signed certificates for developing on local network
    * add script to start local https server
    * add OTA screen to trigger the update
    * make lv_update_label() behave like printf
2020-10-22 fix reboot issue
    * had to disconnect wifi before the soft reboot
    * add git describe tag to OTA screen
    [mqtt_cache.c, velo.c]
2020-10-24 add font-awesome icons + font generation script
    * make measurement rate configurable
    * randomly invert display on boot to mitigate oled burn-in
    * fix off by one bug in fillRect()
    [lv_font.h, velo.c]
2020-10-29 mqtt_cache.c: reliability improvement
    * 2 alternating files to keep the offset pointers
    * if one gets corrupted on write, use the other
    * prevents loosing the complete cache on reconnect after a power cut
    * enable dynamo by default on powerup
    [app_main.c, mqtt_cache.c, velo.c]
2020-11-13 invert wakeup pin polarity
    [velogen2.sch]
2020-11-13 fix 2 C warnings
    [mqtt_cache.c]
2020-11-13 also flip buttons when OLED is rotated
    [velo.c]
2020-11-13 make button flip work
    [velo.c]
2021-09-26 upper_shell: add more clearance for OLED solder pins
    [pcbShell.scad]
2022-03-06 experimenting with LED strips
    disabled MQTT and FLASH chaching for now
2022-07-22 make mqtt work again, fix nasty bug in LED strip code
    [app_main.c, mqtt_cache.c, velo.c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]
2022-07-26 mqtt_cache 💣
2022-07-28 attempt to fix the speed reading, untested
    [app_main.c, mqtt_cache.c, velo.c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]
2022-07-29 fix km/h on oled
    [velo.c]
2022-07-29 fix the freaking touch buttons
    [velo.c]
2024-01-25 port to espressif32@6.5.0
    * compiles, no errors
    * some warnings
    * not tested yet
    [app_main.c, ina219.c, mqtt_cache.c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]
2024-01-28 add some missing files which I forgot to checkin before
    [pcbShell.scad, velogen2.kicad_sch, velogen2.sch]
2024-01-28 replace ws2812 SPI driver with a RMT one
    also fix some depracated warnings.
    Not tested yet.
    [velo.c, velo.h, ws2812.c]
2024-01-29 use espressif led-strip library, make it work
    need 24k resistor and 10 nF to ground on speed_sense pin
2024-01-30 led pattern update
2024-01-31 tune led animation
